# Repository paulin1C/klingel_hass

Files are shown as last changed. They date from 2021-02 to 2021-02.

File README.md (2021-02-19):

# klingel_hass
PCB and code for a small board that intercepts the bell wiring and allows muting and remote door opening with home assistant.
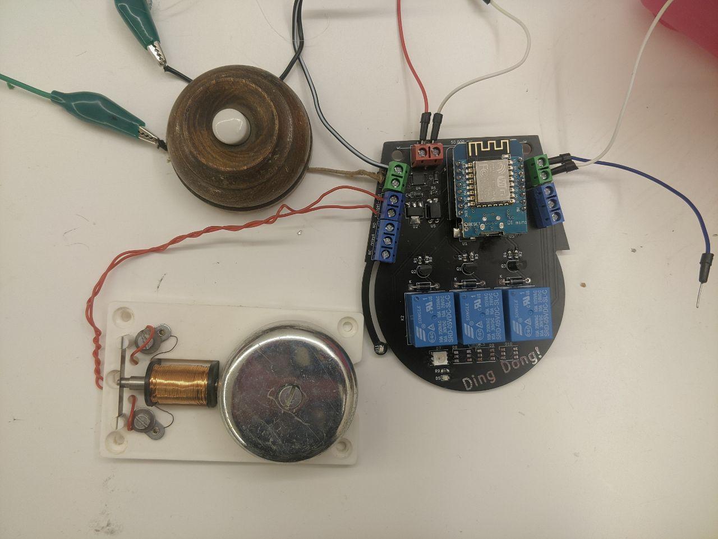
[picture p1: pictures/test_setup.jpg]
<br>
## hardware
### PCB
The gerber and drill files can be found in the `kicad` folder.<br>
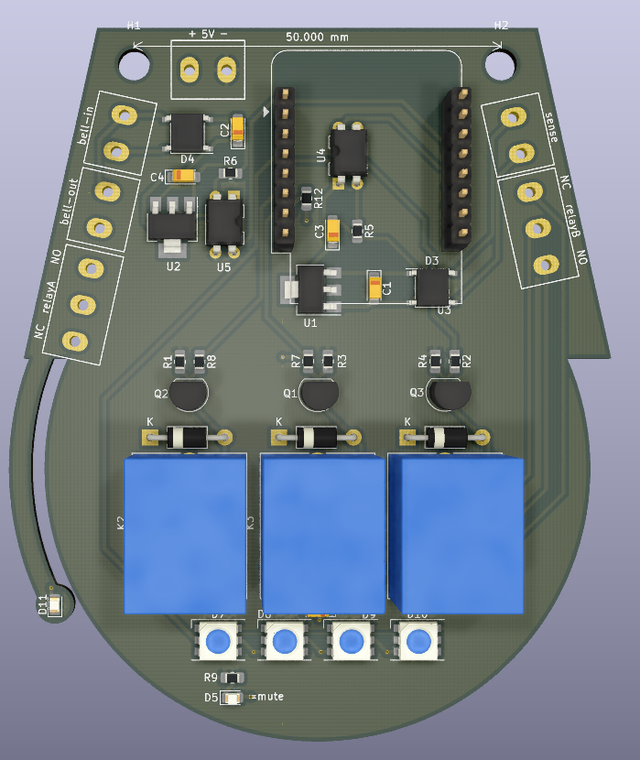
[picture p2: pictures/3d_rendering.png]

### bill of materials
The following parts are used to assemble the PCB:
|reference|part name|value|package|
|---|---|---|---|
|C1-C5|capacitor|10 µF|smd 0805|
|D3,D4|bridge rectifier|ABS10|smd|
|D5,D11|red led||smd 0805|
|D1,D2,D6|diode|1N4007|tht DO-41|
|D7-D10|ws2812 led||smd|
|J1,J3|screw terminal|3 pins|tht 5.08 mm spacing|
|J2,J4,J5,J6|screw terminal|2 pins|tht 5.08 mm spacing|
|K1-K3|relay|5V SPDT|tht|
|Q1-Q3|transistor|BC547|tht TO-92|
|R2,R7,R8,R9,R12|resistor|1K|smd 0805|
|R1,R3,R4|resistor|10K|smd 0805|
|R5,R6|resistor|5|smd 0805|
|U1,U2|voltage regulator|AMS1117-1.5|smd SOT-223-3|
|U3|WEMOS D1 mini||tht|
|U4,U5|optocoupler|PC817|tht|

### connections
If you want to use the muting feature, you will have to cut the wires to your bell.
The voltage of your bell should be between 4V and 16V AC or DC.
A door opener could be connected to one of the relays.
|terminal name|description|
|----|----|
|5V|your 5V power supply (min. 1A)|
|bell-in|wires that normally supply power to your bell|
|bell-out|wires going to your bell|
|sense|additional input to detect voltage (4-16V AC or DC)|
|relayA,B|relay (NC = normally closes, NO = normally open)|

## software
I used esphome as a simple way to use the device with home assistant.

### configuration
Just change into the esphome directory, copy `secrets_example.yaml` to `secrets.yaml` and change its options accordingly.

### firmware upload
The firmware needs to be compiled with `esphome klingel_hass.yaml compile` and uploaded to a connected WEMOS D1 mini board with `esphome klingel_hass.yaml upload`.

### auto mute
A friend was worried about what would happen, when the device looses connection or gets stuck in a boot loop, while the bell was muted. So when auto mute is enabled, the bell stays connected/unmuted until a ring is detected and is only separating the bell connection, when the bell should be ringing. Depending on your bell, you might still hear a short ring until the relay opens.

## home assistant
The device should connect to wifi and be discovered by home assistant, which will ask you for the api password in `esphome/secrets.yaml` to connect.
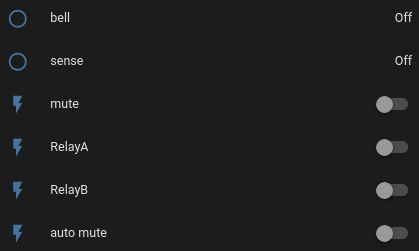
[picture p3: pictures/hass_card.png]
<br>

### entities
|name|description|
|---|---|
|bell|changes to `on` when the bell is or should be ringing|
|sense|changes to `on` when a voltage is detected on the sense input|
|mute|mutes the bell when switched on|
|relayA|controls relay A|
|relayB|controls relay B|
|auto mute|controls auto mute feature|
|led|controls the small red led on the left|
|ws28|should control the ws2812 leds (untested)|

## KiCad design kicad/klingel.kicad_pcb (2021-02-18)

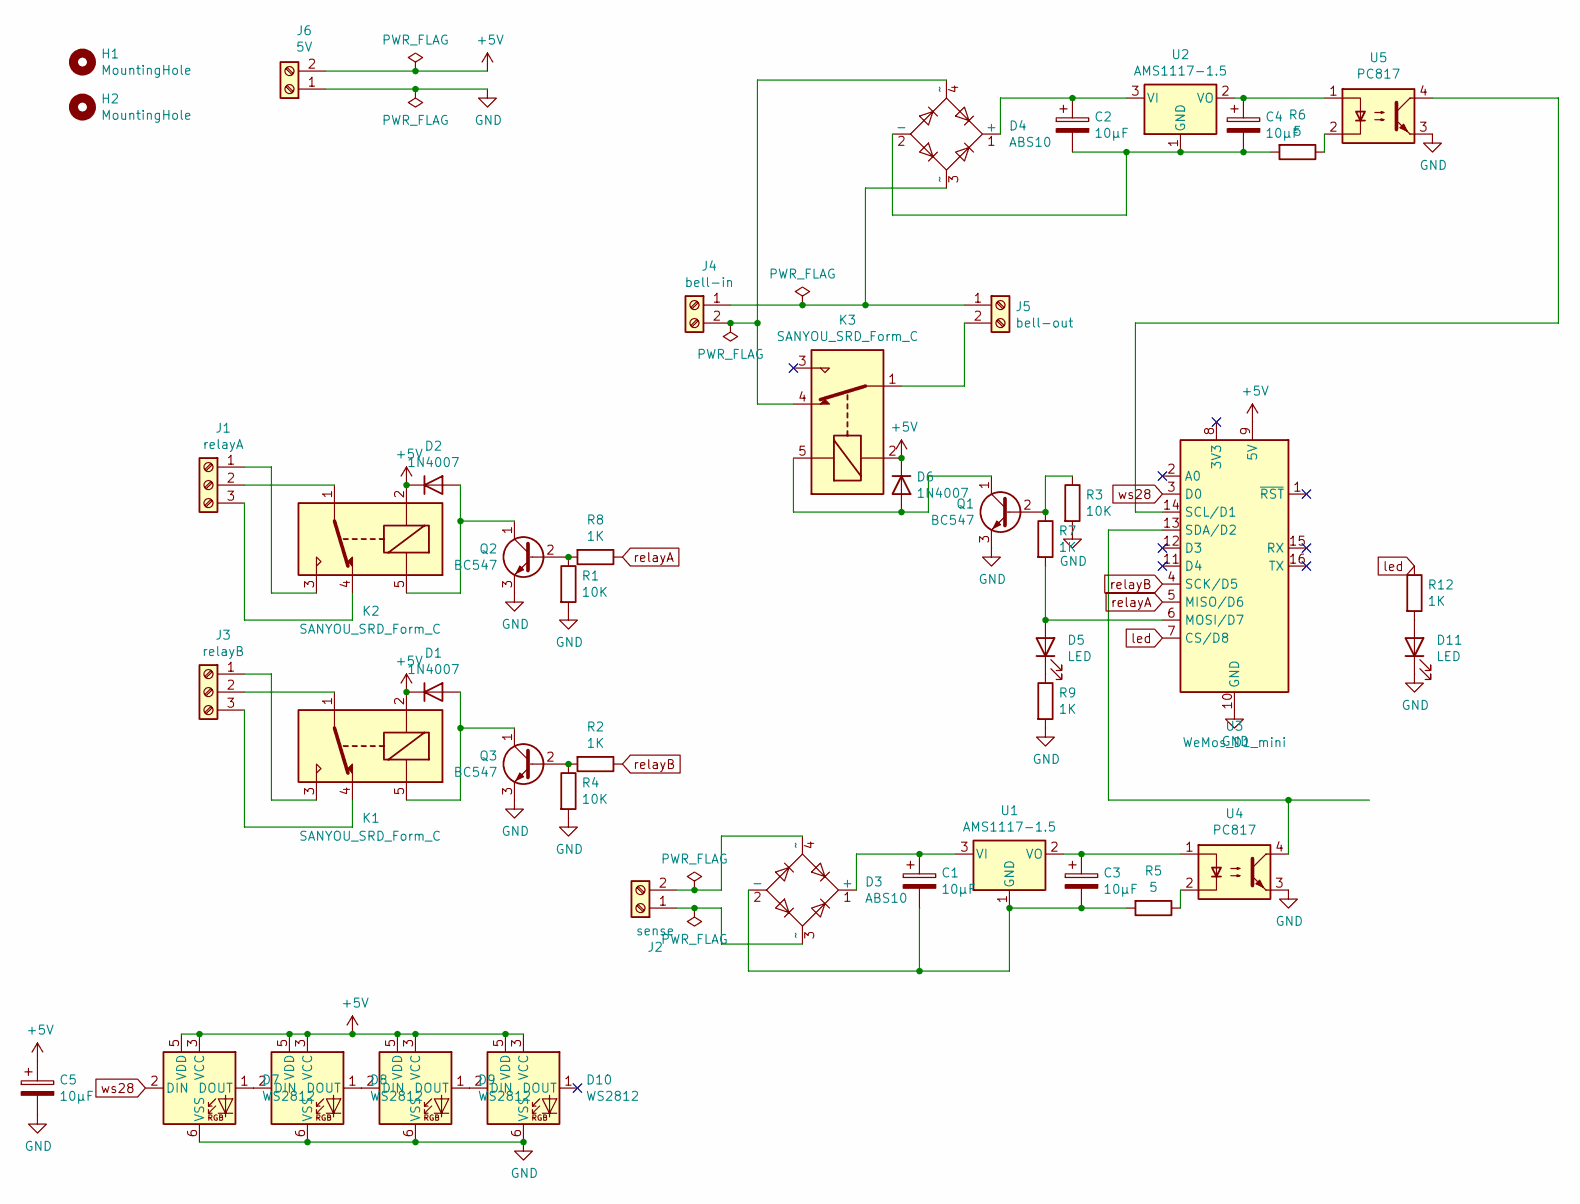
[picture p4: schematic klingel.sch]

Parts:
C1, C2, C3, C4, C5: 10µF; CP_EIA-3216-18_Kemet-A_Pad1.58x1.35mm_HandSolder
D1, D2, D6: 1N4007; D_DO-41_SOD81_P10.16mm_Horizontal
D3, D4: ABS10; Diode_Bridge_Diotec_ABS
D5, D11: LED; LED_0805_2012Metric
D7, D8, D9, D10: WS2812; LED_WS2812_PLCC6_5.0x5.0mm_P1.6mm
H1, H2: MountingHole; MountingHole_4.3mm_M4
J1: relayA; terminal_3pin
J2: sense; termina_2pin
J3: relayB; terminal_3pin
J4: bell-in; termina_2pin
J5: bell-out; termina_2pin
J6: 5V; termina_2pin
K1, K2, K3: SANYOU_SRD_Form_C; Relay_SPDT_SANYOU_SRD_Series_Form_C
Q1, Q2, Q3: BC547; TO-92_Inline
R1, R3, R4: 10K; R_0805_2012Metric_Pad1.20x1.40mm_HandSolder
R2, R7, R8, R9, R12: 1K; R_0805_2012Metric_Pad1.20x1.40mm_HandSolder
R5, R6: 5; R_0805_2012Metric_Pad1.20x1.40mm_HandSolder
U1, U2: AMS1117-1.5; SOT-223-3_TabPin2
U3: WeMos_D1_mini; WEMOS_D1_mini_light
U4, U5: PC817; DIP-4_W7.62mm

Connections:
+5V: C5.1, D1.1 (K), D2.1 (K), D6.1 (K), D7.3 (VCC), D7.5 (VDD), D8.3 (VCC), D8.5 (VDD), D9.3 (VCC), D9.5 (VDD), D10.3 (VCC), D10.5 (VDD), J6.2, K1.2, K2.2, K3.2, U3.9 (5V)
GND: C5.2, D7.6 (VSS), D8.6 (VSS), D9.6 (VSS), D10.6 (VSS), D11.1 (K), J6.1, Q1.3 (E), Q2.3 (E), Q3.3 (E), R1.2, R3.2, R4.2, R9.2, U3.10 (GND), U4.3, U5.3
unnamed: C1.1, D3.1 (+), U1.3 (VI)
unnamed: C1.2, C3.2, D3.2 (-), R5.2, U1.1 (GND)
unnamed: C2.1, D4.1 (+), U2.3 (VI)
unnamed: C2.2, C4.2, D4.2 (-), R6.2, U2.1 (GND)
unnamed: C3.1, U1.2 (VO), U4.1
unnamed: C4.1, U2.2 (VO), U5.1
unnamed: D1.2 (A), K1.5, Q3.1 (C)
unnamed: D2.2 (A), K2.5, Q2.1 (C)
unnamed: D3.3 (~~), J2.1
unnamed: D3.4 (~~), J2.2
unnamed: D4.3 (~~), J4.1, J5.1
unnamed: D4.4 (~~), J4.2, K3.4
unnamed: D5.1 (K), R9.1
unnamed: D5.2 (A), R7.2, U3.6 (MOSI/D7)
unnamed: D6.2 (A), K3.5, Q1.1 (C)
unnamed: D7.1 (DOUT), D8.2 (DIN)
unnamed: D8.1 (DOUT), D9.2 (DIN)
unnamed: D9.1 (DOUT), D10.2 (DIN)
unnamed: D11.2 (A), R12.2
unnamed: J1.1, K2.3
unnamed: J1.2, K2.1
unnamed: J1.3, K2.4
unnamed: J3.1, K1.3
unnamed: J3.2, K1.1
unnamed: J3.3, K1.4
unnamed: J5.2, K3.1
unnamed: Q1.2 (B), R3.1, R7.1
unnamed: Q2.2 (B), R1.1, R8.2
unnamed: Q3.2 (B), R2.2, R4.1
unnamed: R5.1, U4.2
unnamed: R6.1, U5.2
unnamed: U3.13 (SDA/D2), U4.4
unnamed: U3.14 (SCL/D1), U5.4
led: R12.1, U3.7 (CS/D8)
relayA: R8.1, U3.5 (MISO/D6)
relayB: R2.1, U3.4 (SCK/D5)
ws28: D7.2 (DIN), U3.3 (D0)

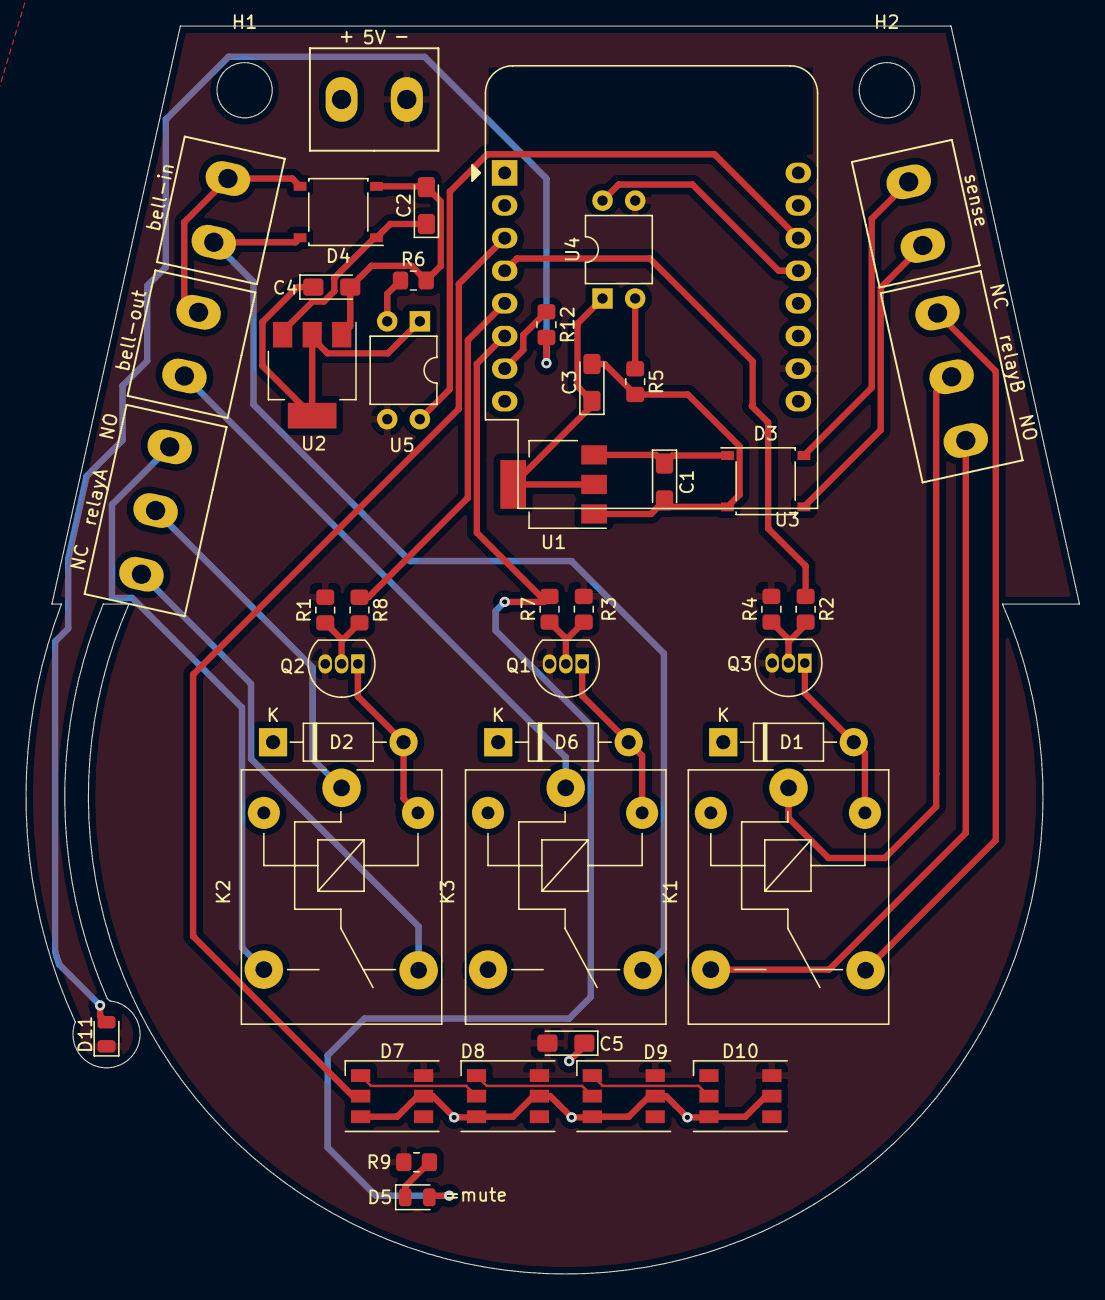
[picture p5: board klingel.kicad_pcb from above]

Board: 2 copper layers, 82.0 x 97.2 mm, 45 parts (0 on the bottom side), 39 nets.
